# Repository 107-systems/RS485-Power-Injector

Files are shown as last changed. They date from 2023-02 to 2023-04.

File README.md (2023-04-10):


`RS485-Power-Injector`
======================


This repository contains the design files for [L3X-Z](https://github.com/107-systems/l3xz)'s RS485 power injector which allows to directly inject battery power into the RS485 bus connecting the robot's Dynamixel MX-28AR servos.

<p align="center">
  
</p>

<p align="center">
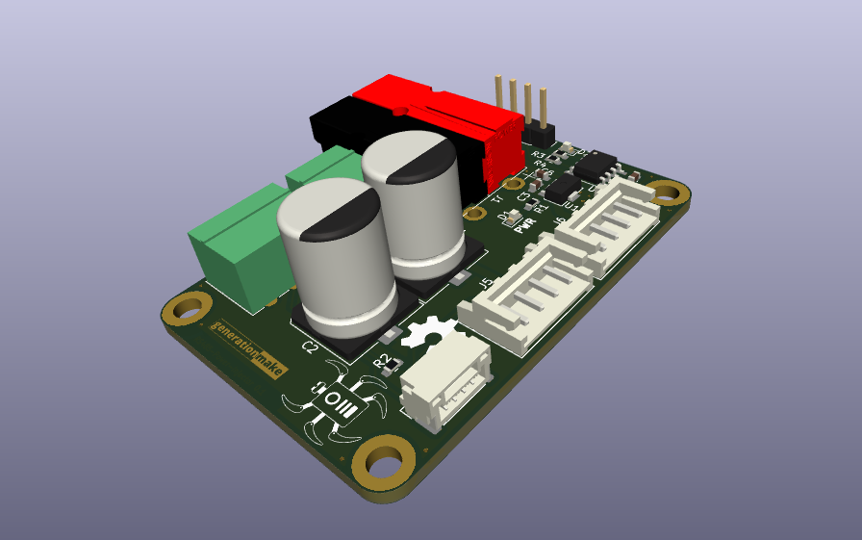
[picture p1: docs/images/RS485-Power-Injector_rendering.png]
  
</p>

## Debug circuitry

This board contains a circuit with a RS485 driver to drive a LED to show bus activity. This circuit can also be used to interface the RS485 bus to a controller or computer. The circuit can be used with 3.3V and 5V levels. Some parts need to be changed to achieve this.

| **Designator** | **3.3V version** | **5V version** |
|:---:|:---:|:---:|
| U1 | L78L33ACUTR | L78L05ACUTR |
| U2 | SP3485EN-L | SN75176AD |

## Connectors

### Power Input J1
Anderson Power Pole

| **Pin** | **Signal** | **Description** |
|:---:|:---:|:---:|
| 1 | +BATT | Directly to Dynamixel |
| 2 | GND | |

The input voltage is directly feed to the Dynamixel servo. So the maximum voltage depends solely on the servo used.

### Power Input J2
Würth WR-TBL 3.5mm 2-pin screw terminal.

| **Pin** | **Signal** | **Description** |
|:---:|:---:|:---:|
| 1 | +BATT | Directly to Dynamixel |
| 2 | GND | |

### RS485 Input J3
Würth WR-TBL 3.5mm 3-pin screw terminal.

| **Pin** | **Signal** | **Description** |
|:---:|:---:|:---:|
| 1 | RS485-A | Directly to Dynamixel |
| 2 | RS485-B | Directly to Dynamixel |
| 3 | GND | |

### RS485 Input J4
JST GH 1.25mm 4-pin.

| **Pin** | **Signal** | **Description** |
|:---:|:---:|:---:|
| 1 | +BATT | to Dynamixel via R2 |
| 2 | RS485-A | Directly to Dynamixel |
| 3 | RS485-B | Directly to Dynamixel |
| 4 | GND | |

### Dynamixel connectors J5 and J6
In the Dynamixel world there exist two type of connectors: [Molex Mini-SPOX](https://www.molex.com/molex/products/part-detail/pcb_headers/0022035045) and [JST EH](https://www.jst-mfg.com/product/pdf/eng/eEH.pdf).

Both are 2.5 mm pitch and use the same pin out and both can be mounted on the board. So you can decide which one to use and which fits your application and servo.

| **Pin** | **Signal** | **Description** |
|:---:|:---:|:---:|
| 1 | GND | |
| 2 | +BATT | |
| 3 | RS485-A | |
| 4 | RS485-B | |

### RS485 Debug output J7
Pin header 2.54mm 4-pin.

| **Pin** | **Signal** | **Description** |
|:---:|:---:|:---:|
| 1 | RS485_TXEN | |
| 2 | RS485_TX | |
| 3 | RS485_RX | |
| 4 | GND | |

## Enclosure

There exists a 3D printable enclosure to encapsulate the PCB.

### Standard

<p align="center">
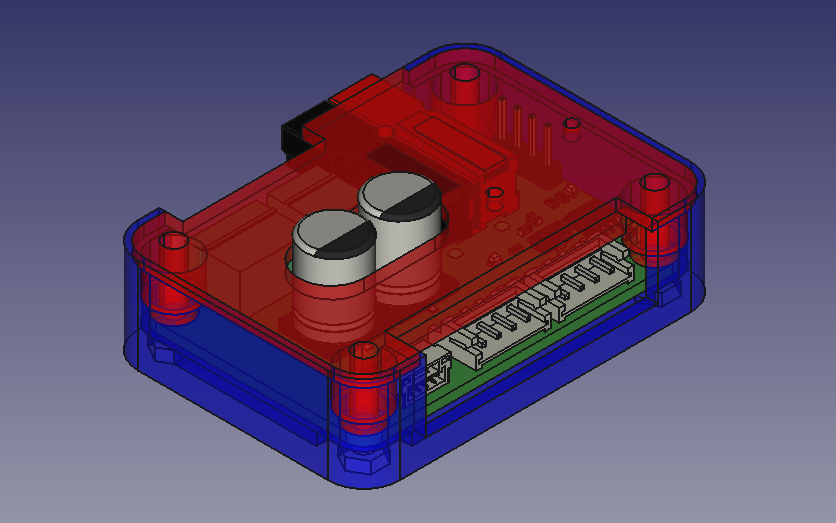
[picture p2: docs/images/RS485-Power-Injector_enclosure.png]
  
</p>

## PCB
### Top
<p align="center">
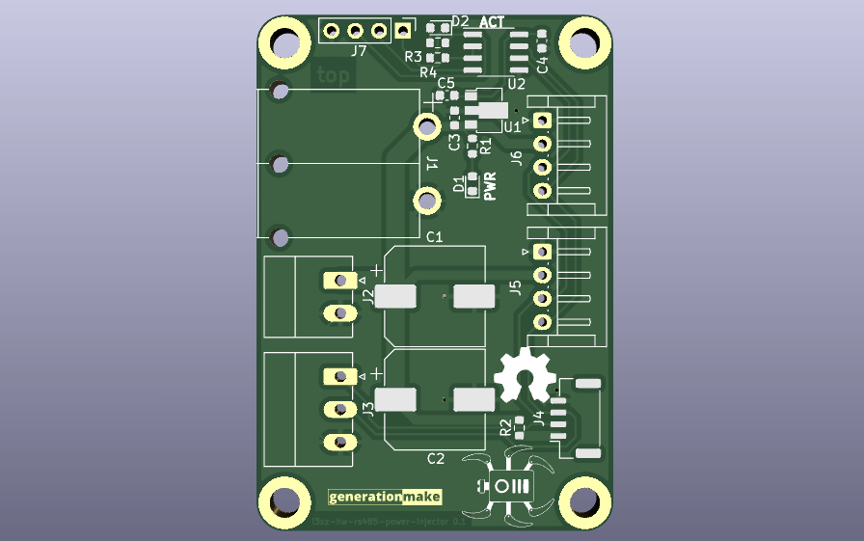
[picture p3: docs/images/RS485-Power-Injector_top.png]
  
</p>

### Bottom
<p align="center">
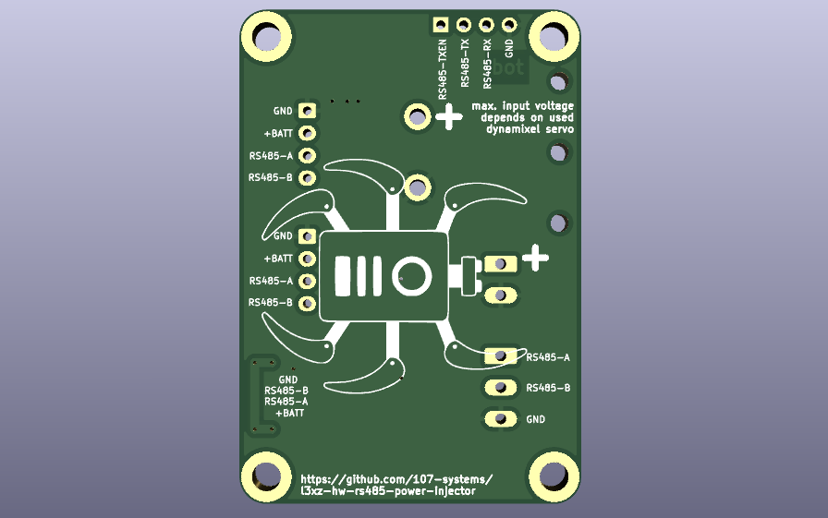
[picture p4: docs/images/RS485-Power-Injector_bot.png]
  
</p>

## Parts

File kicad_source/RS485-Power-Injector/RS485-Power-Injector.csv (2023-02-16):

Source: | /home/bernhard/projects/RS485-Power-Injector/kicad_source/RS485-Power-Injector/RS485-Power-Injector.kicad_sch
Date: | Mo 23 Jan 2023 17:53:04 CET
Tool: | Eeschema 6.0.10-86aedd382b~118~ubuntu22.04.1
Generator: | /usr/share/kicad/plugins/bom_csv_grouped_by_value.py
Component Count: | 20
Individual Components:
Item | Qty | Reference(s) | Value | LibPart | Footprint | Datasheet
 |  | C1 | 220 uF / 50 V | Device:C_Polarized | Capacitor_SMD:CP_Elec_10x14.3 | ~
 |  | C2 | 220 uF / 50 V | Device:C_Polarized | Capacitor_SMD:CP_Elec_10x14.3 | ~
 |  | C3 | 100 nF | Device:C_Small | Capacitor_SMD:C_0603_1608Metric | ~
 |  | C4 | 100 nF | Device:C_Small | Capacitor_SMD:C_0603_1608Metric | ~
 |  | C5 | 1 uF | Device:C_Small | Capacitor_SMD:C_0603_1608Metric | ~
 |  | D1 | LED green | Device:LED_Small | LED_SMD:LED_0603_1608Metric | ~
 |  | D2 | LED green | Device:LED_Small | LED_SMD:LED_0603_1608Metric | ~
 |  | J1 | PowerPole | Connector_Generic:Conn_01x02 | generationmake:POWERPOLE_hor_2 | ~
 |  | J2 | DNI | Connector_Generic:Conn_01x02 | Connector_Phoenix_MC:PhoenixContact_MC_1,5_2-G-3.5_1x02_P3.50mm_Horizontal | ~
 |  | J3 | DNI | Connector_Generic:Conn_01x03 | Connector_Phoenix_MC:PhoenixContact_MC_1,5_3-G-3.5_1x03_P3.50mm_Horizontal | ~
 |  | J4 | SM04B-GHS-TB | Connector_Generic_MountingPin:Conn_01x04_MountingPin | Connector_JST:JST_GH_SM04B-GHS-TB_1x04-1MP_P1.25mm_Horizontal | ~
 |  | J5 | EH_S4B-EH | Connector_Generic:Conn_01x04 | Connector_JST:JST_EH_S4B-EH_1x04_P2.50mm_Horizontal | ~
 |  | J6 | EH_S4B-EH | Connector_Generic:Conn_01x04 | Connector_JST:JST_EH_S4B-EH_1x04_P2.50mm_Horizontal | ~
 |  | J7 | DNI | Connector_Generic:Conn_01x04 | Connector_PinHeader_2.54mm:PinHeader_1x04_P2.54mm_Vertical | ~
 |  | R1 | 10k | Device:R_Small | Resistor_SMD:R_0603_1608Metric | ~
 |  | R2 | DNI | Device:R_Small | Resistor_SMD:R_0603_1608Metric | ~
 |  | R3 | 10k | Device:R_Small | Resistor_SMD:R_0603_1608Metric | ~
 |  | R4 | 10k | Device:R_Small | Resistor_SMD:R_0603_1608Metric | ~
 |  | U1 | L78L05_SOT89 | Regulator_Linear:L78L05_SOT89 | Package_TO_SOT_SMD:SOT-89-3 | http://www.st.com/content/ccc/resource/technical/document/datasheet/15/55/e5/aa/23/5b/43/fd/CD00000446.pdf/files/CD00000446.pdf/jcr:content/translations/en.CD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
 |  | U2 | SN75176AD | Interface_UART:SN75176AD | Package_SO:SOIC-8_3.9x4.9mm_P1.27mm | http://www.ti.com/lit/ds/symlink/sn75176a.pdf
Collated Components:
Item | Qty | Reference(s) | Value | LibPart | Footprint | Datasheet
1 | 2 | C1, C2 | 220 uF / 50 V | Device:C_Polarized | Capacitor_SMD:CP_Elec_10x14.3 | ~
2 | 2 | C3, C4 | 100 nF | Device:C_Small | Capacitor_SMD:C_0603_1608Metric | ~
3 | 1 | C5 | 1 uF | Device:C_Small | Capacitor_SMD:C_0603_1608Metric | ~
4 | 2 | D1, D2 | LED green | Device:LED_Small | LED_SMD:LED_0603_1608Metric | ~
5 | 1 | J1 | PowerPole | Connector_Generic:Conn_01x02 | generationmake:POWERPOLE_hor_2 | ~
6 | 1 | J2 | DNI | Connector_Generic:Conn_01x02 | Connector_Phoenix_MC:PhoenixContact_MC_1,5_2-G-3.5_1x02_P3.50mm_Horizontal | ~
7 | 1 | J3 | DNI | Connector_Generic:Conn_01x03 | Connector_Phoenix_MC:PhoenixContact_MC_1,5_3-G-3.5_1x03_P3.50mm_Horizontal | ~
8 | 1 | J4 | SM04B-GHS-TB | Connector_Generic_MountingPin:Conn_01x04_MountingPin | Connector_JST:JST_GH_SM04B-GHS-TB_1x04-1MP_P1.25mm_Horizontal | ~
9 | 2 | J5, J6 | EH_S4B-EH | Connector_Generic:Conn_01x04 | Connector_JST:JST_EH_S4B-EH_1x04_P2.50mm_Horizontal | ~
10 | 1 | J7 | DNI | Connector_Generic:Conn_01x04 | Connector_PinHeader_2.54mm:PinHeader_1x04_P2.54mm_Vertical | ~
11 | 3 | R1, R3, R4 | 10k | Device:R_Small | Resistor_SMD:R_0603_1608Metric | ~
12 | 1 | R2 | DNI | Device:R_Small | Resistor_SMD:R_0603_1608Metric | ~
13 | 1 | U1 | L78L05_SOT89 | Regulator_Linear:L78L05_SOT89 | Package_TO_SOT_SMD:SOT-89-3 | http://www.st.com/content/ccc/resource/technical/document/datasheet/15/55/e5/aa/23/5b/43/fd/CD00000446.pdf/files/CD00000446.pdf/jcr:content/translations/en.CD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
14 | 1 | U2 | SN75176AD | Interface_UART:SN75176AD | Package_SO:SOIC-8_3.9x4.9mm_P1.27mm | http://www.ti.com/lit/ds/symlink/sn75176a.pdf

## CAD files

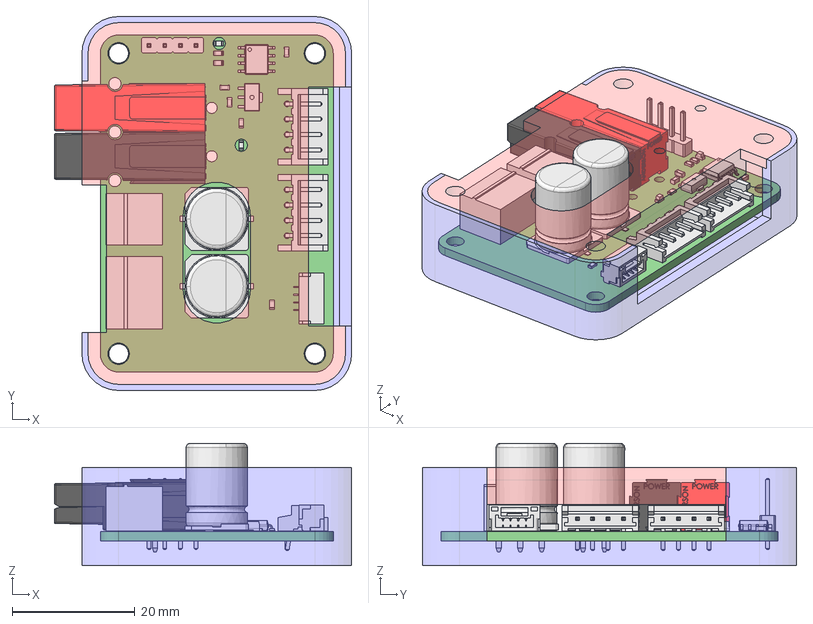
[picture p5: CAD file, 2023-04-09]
freecad_source/enclosure_lp.FCStd
48.5 x 61.0 x 20.0 mm
bottom
top
RS485-Power-Injector PCB

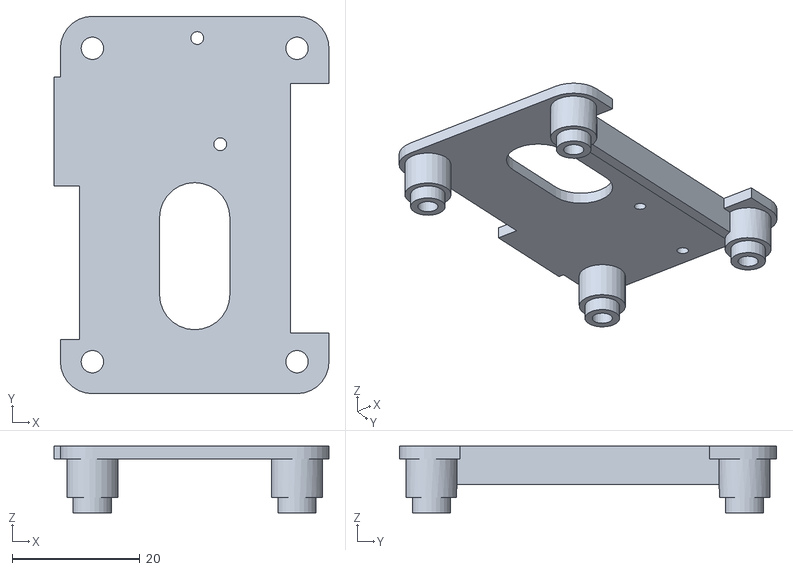
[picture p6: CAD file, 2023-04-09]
production_data/enclosure_lp-top.stl
43.0 x 59.0 x 10.4

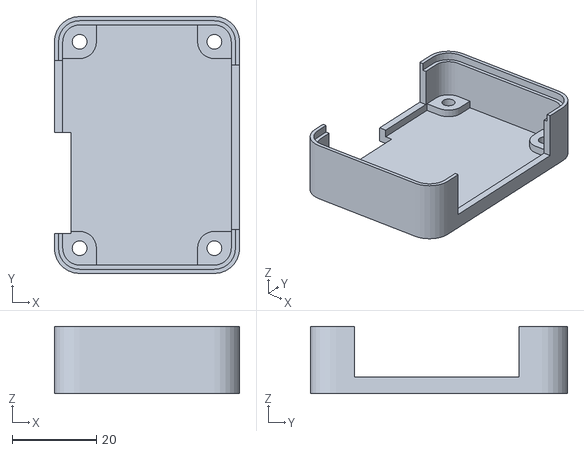
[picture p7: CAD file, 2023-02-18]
production_data/enclosure_lp-bottom.stl
44.0 x 61.0 x 16.0

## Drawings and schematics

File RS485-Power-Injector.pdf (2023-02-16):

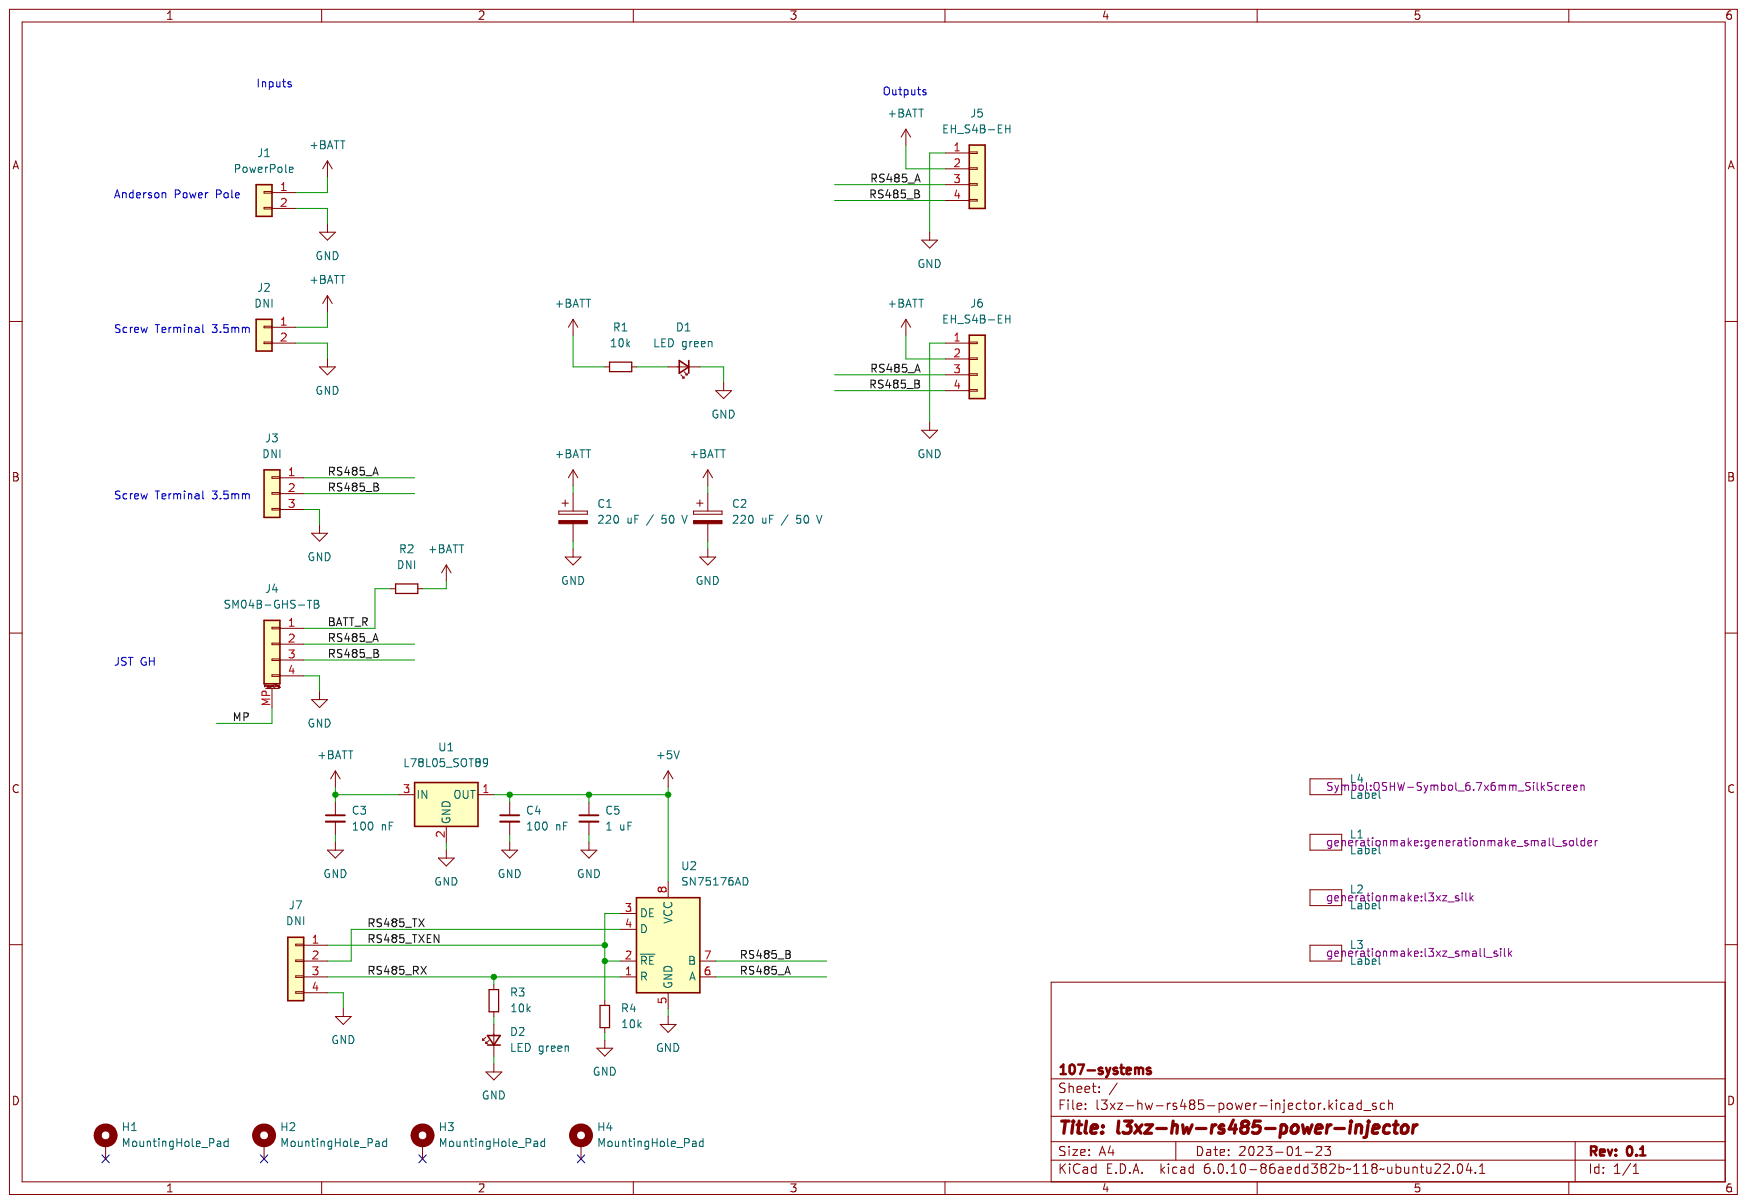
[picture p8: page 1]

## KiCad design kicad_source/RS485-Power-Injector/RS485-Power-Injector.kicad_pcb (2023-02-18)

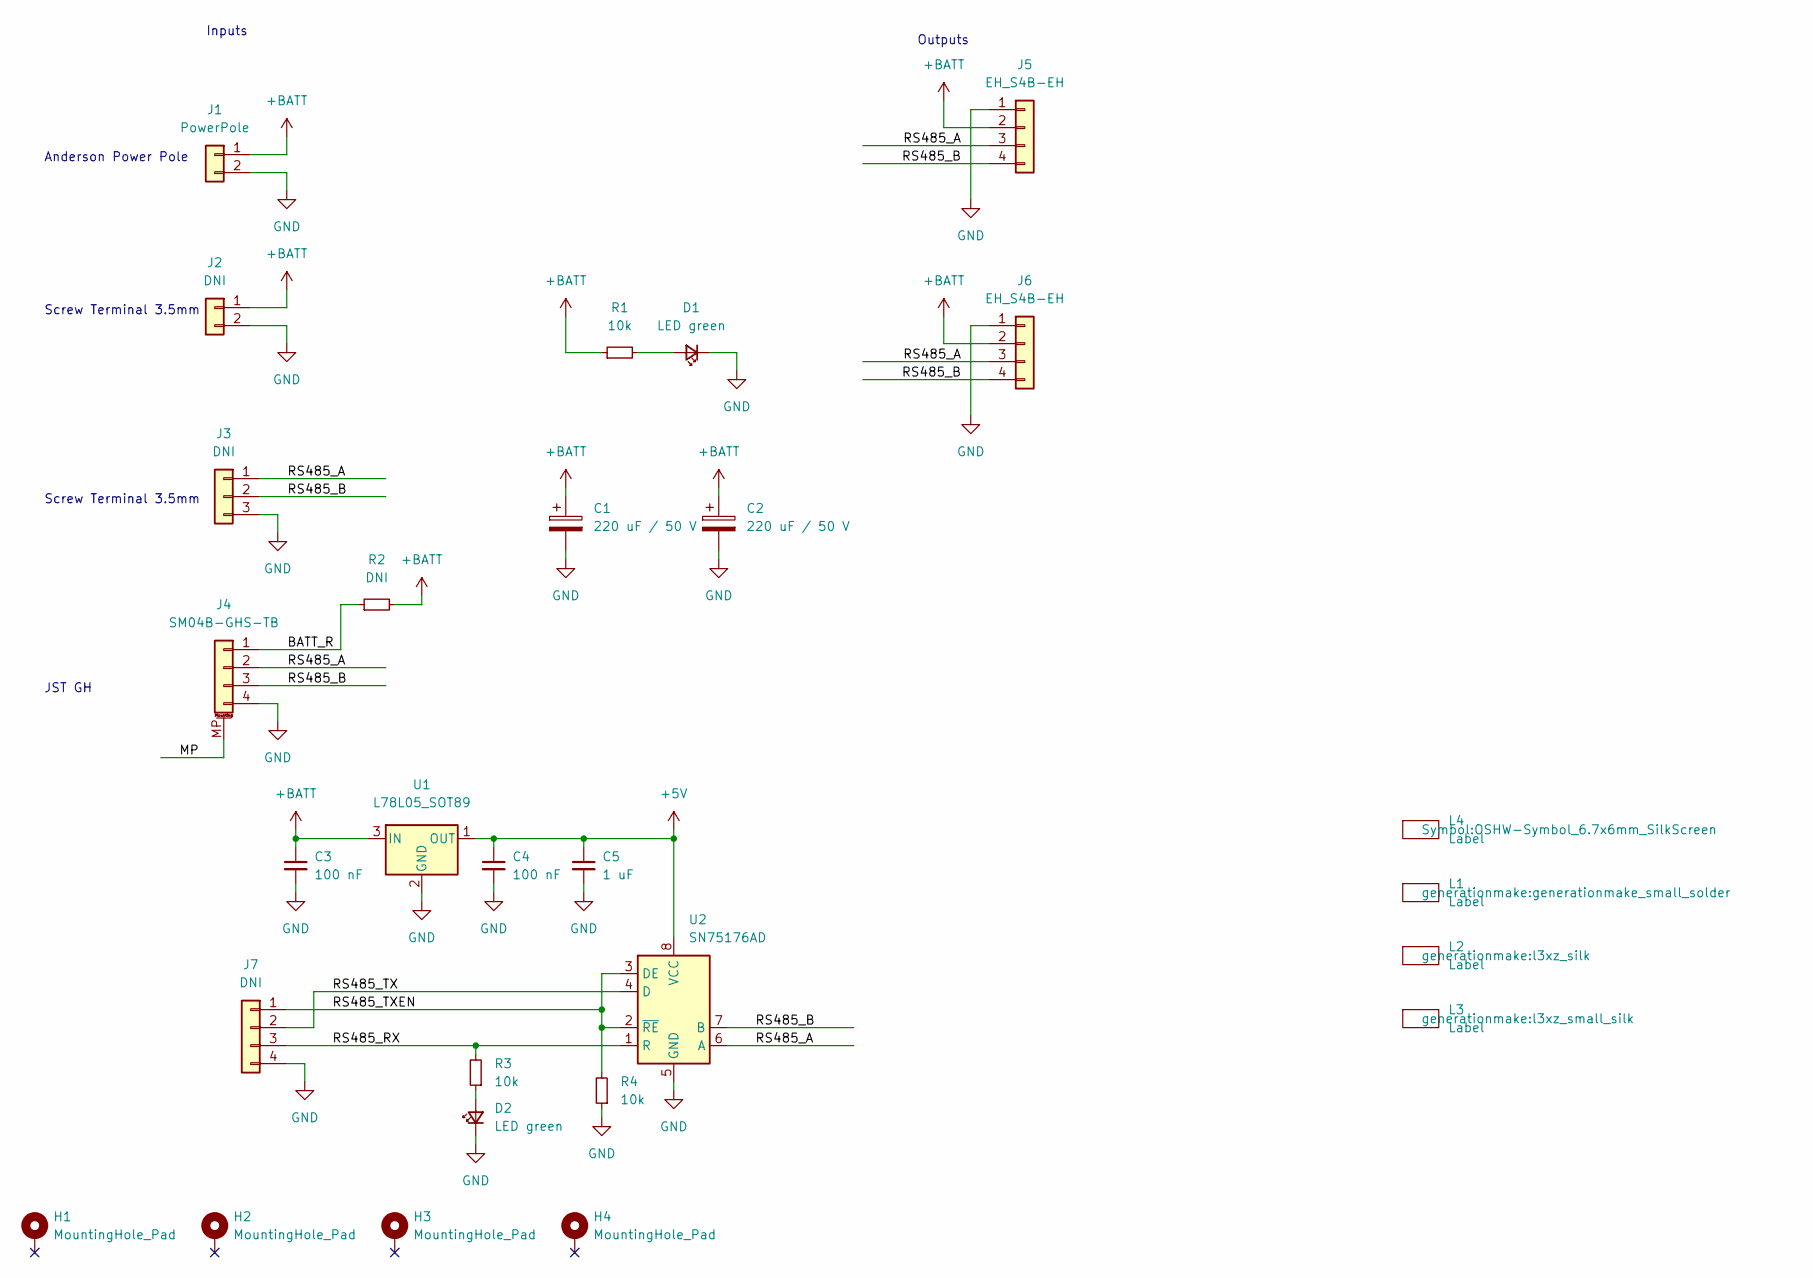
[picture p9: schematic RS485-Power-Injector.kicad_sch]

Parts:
C1, C2: 220 uF / 50 V; CP_Elec_10x14.3
C3, C4: 100 nF; C_0603_1608Metric
C5: 1 uF; C_0603_1608Metric
D1, D2: LED green; LED_0603_1608Metric
H1, H2, H3, H4: MountingHole_Pad; MountingHole_3.2mm_M3_DIN965_Pad
J1: PowerPole; POWERPOLE_hor_2
J2: DNI; PhoenixContact_MC_1,5_2-G-3.5_1x02_P3.50mm_Horizontal
J3: DNI; PhoenixContact_MC_1,5_3-G-3.5_1x03_P3.50mm_Horizontal
J4: SM04B-GHS-TB; JST_GH_SM04B-GHS-TB_1x04-1MP_P1.25mm_Horizontal
J5, J6: EH_S4B-EH; JST_EH_S4B-EH_1x04_P2.50mm_Horizontal
J7: DNI; PinHeader_1x04_P2.54mm_Vertical
L1: Label; generationmake_small_solder
L2: Label; l3xz_silk
L3: Label; l3xz_small_silk
L4: Label; OSHW-Symbol_6.7x6mm_SilkScreen
R1, R3, R4: 10k; R_0603_1608Metric
R2: DNI; R_0603_1608Metric
U1: L78L05_SOT89; SOT-89-3
U2: SN75176AD; SOIC-8_3.9x4.9mm_P1.27mm

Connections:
+5V: C4.1, C5.1, U1.1 (OUT), U2.8 (VCC)
+BATT: C1.1, C2.1, C3.1, J1.1, J2.1, J5.2, J6.2, R1.1, R2.2, U1.3 (IN)
/BATT_R: J4.1, R2.1
/MP: J4.MP (MountPin)
/RS485_A: J3.1, J4.2, J5.3, J6.3, U2.6 (A)
/RS485_B: J3.2, J4.3, J5.4, J6.4, U2.7 (B)
/RS485_RX: J7.3, R3.2, U2.1 (R)
/RS485_TX: J7.2, U2.4 (D)
/RS485_TXEN: J7.1, R4.2, U2.2 (~RE), U2.3 (DE)
GND: C1.2, C2.2, C3.2, C4.2, C5.2, D1.1 (K), D2.1 (K), J1.2, J2.2, J3.3, J4.4, J5.1, J6.1, J7.4, R4.1, U1.2 (GND), U2.5 (GND)
unnamed: D1.2 (A), R1.2
unnamed: D2.2 (A), R3.1

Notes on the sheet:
JST GH
Outputs
Anderson Power Pole
Screw Terminal 3.5mm
Inputs

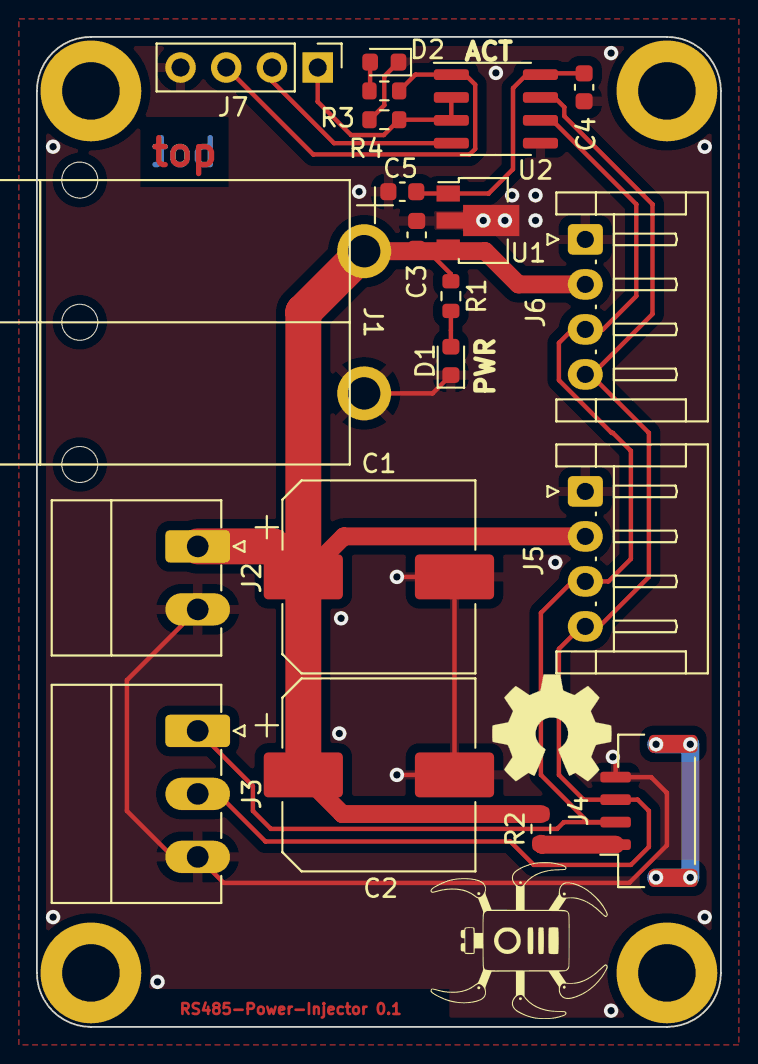
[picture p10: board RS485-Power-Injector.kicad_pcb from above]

Board: 2 copper layers, 38.0 x 55.0 mm, 28 parts (1 on the bottom side), 11 nets.

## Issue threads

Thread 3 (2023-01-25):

clearify dynamixel connectors

generationmake, 2023-01-25:
<a href="https://107-systems.org/">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</a>

### ⚡ Feature Request

There exist several connector types in the dynamixel world.

MX-28 uses Molex Mini-SPOX: https://www.molex.com/molex/products/part-detail/pcb_headers/0022035045
U2D2 uses JST EH connectors: https://www.jst-mfg.com/product/pdf/eng/eEH.pdf

both are 2.5 mm pitch and seem to use the same pin out.

It seems like both connectors could be mounted on the board.

aentinger, 2023-01-26:
If possible, why not? 👍

generationmake, 2023-01-29:
https://www.reichelt.de/molex-stiftleiste-90-mini-spox-1x4-polig-stecker-molex-22057045-p185735.html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

generationmake, 2023-01-29:
https://www.conrad.de/de/p/jst-stiftleiste-standard-eh-polzahl-gesamt-4-s4b-eh-lf-sn-1-st-1217330.html

aentinger, 2023-02-18:
Hi @generationmake ☕ 👋

> https://www.conrad.de/de/p/jst-stiftleiste-standard-eh-polzahl-gesamt-4-s4b-eh-lf-sn-1-st-1217330.html

Is this footprint also available on the board?

generationmake, 2023-02-18:
Hi @aentinger
Both connectors (JST EH and Molex Mini Spox) should fit to J5 und J6 because both have 2.5 mm pitch.
You can place whatever you like.
I will update the readme and clearify this.

Closed 2023-04-09.

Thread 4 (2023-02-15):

[Feature Request] Design a 3D printable case for the RS485 Power Injector

aentinger, 2023-02-15:
<a href="https://107-systems.org/">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</a>

### ⚡ Feature Request

Hi @generationmake :coffee: :wave: Can you please design a 3D printable case for the RS485 Power Injector :bow: ?

Closed 2023-02-18.

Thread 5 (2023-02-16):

[Feature Request] check 3.3 V compatibility

generationmake, 2023-02-16:
<a href="https://107-systems.org/">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</a>

### ⚡ Feature Request

The power injector has a TTL interface. At the moment this works with 5 V levels.

Maybe it is possible to change this to 3.3 V levels with a placement option. Voltage regulator and RS485 driver should be affected.

Closed 2023-04-10.

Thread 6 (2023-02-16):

[Bug Report] clearance of screw terminal

generationmake, 2023-02-16:
<a href="https://107-systems.org/">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</a>

### :bug: Bug Report

the clearance of screw terminals is not enough if plugable connectors are used. They collide with the PCB.

Place connectors closer to the edge of the PCB.

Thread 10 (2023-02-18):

[Feature Request] Integrate hole for receive LED in case redesign

aentinger, 2023-02-18:
<a href="https://107-systems.org/">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</a>

### ⚡ Feature Request

Please integrate a opening in the top enclosure so that the receive LED is visible from the outside.

Closed 2023-04-09.

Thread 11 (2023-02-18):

[Feature Request] Close-off currently open spaces in enclosure

aentinger, 2023-02-18:
<a href="https://107-systems.org/">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</a>

### ⚡ Feature Request

In a enclosure re-design the currently open spaces in the enclosure should be closed by downward facing lips from the top enclosure.

Closed 2023-04-09.

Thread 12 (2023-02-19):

[Feature Request] Reduce frequency of bus acitivity LED

aentinger, 2023-02-19:
<a href="https://107-systems.org/">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</a>

### ⚡ Feature Request

The [U2D2](https://emanual.robotis.com/docs/en/parts/interface/u2d2/) probably uses a LED only on the DE/nRE pin which toogles considerably less often than the bits on the data line. Maybe we can consider something like this or a pre-scaler, at any rate the LED is currently ON all the time, regardless of bus activity.

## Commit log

2023-01-07 added kicad project
    [l3xz-hw-rs485-power-injector.kicad_pcb, l3xz-hw-rs485-power-injector.kicad_sch]
2023-01-07 updated pcb
    [l3xz-hw-rs485-power-injector.kicad_pcb, l3xz-hw-rs485-power-injector.kicad_sch]
2023-01-08 added schematic pdf
2023-01-21 added resistor to connect JST GH connector to +BATT
    [l3xz-hw-rs485-power-injector.kicad_pcb, l3xz-hw-rs485-power-injector.kicad_sch]
2023-01-21 added RS-485 transceiver and status LED
    [l3xz-hw-rs485-power-injector.kicad_pcb, l3xz-hw-rs485-power-injector.kicad_sch]
2023-01-21 added mounting pad on JST GH connector
    [l3xz-hw-rs485-power-injector.kicad_pcb, l3xz-hw-rs485-power-injector.kicad_sch]
2023-01-21 added some labels
    [l3xz-hw-rs485-power-injector.kicad_pcb, l3xz-hw-rs485-power-injector.kicad_sch]
2023-01-21 updated schematic pdf and images
2023-01-23 generated BOM
    [l3xz-hw-rs485-power-injector.csv, l3xz-hw-rs485-power-injector.kicad_sch]
2023-01-23 added some gnd vias
    [l3xz-hw-rs485-power-injector.kicad_pcb]
2023-02-16 Rename from l3xz-hw-rs485-power-injector to RS485-Power-Injector. (#7)
    [RS485-Power-Injector.csv, RS485-Power-Injector.kicad_pcb, RS485-Power-Injector.kicad_sch]
2023-02-16 Fix CI spell check action. (#8)
    Exclude kicad_source folder from spell checking.
2023-02-16 updated footprints, generated step file
    [RS485-Power-Injector.kicad_pcb]
2023-02-16 added freecad project and first draft of enclosure
    [enclosure_lp.FCStd]
2023-02-16 updated dimensions
    [enclosure_lp.FCStd]
2023-02-16 added stl production data and image of enclosure
    [enclosure_lp-bottom.stl, enclosure_lp-top.stl]
2023-04-09 updated readme with dynamixel connector info
2023-04-09 added holes for LEDs
    [enclosure_lp.FCStd]
2023-04-09 added lid over connectors, updated stl file
    [enclosure_lp-top.stl, enclosure_lp.FCStd]
